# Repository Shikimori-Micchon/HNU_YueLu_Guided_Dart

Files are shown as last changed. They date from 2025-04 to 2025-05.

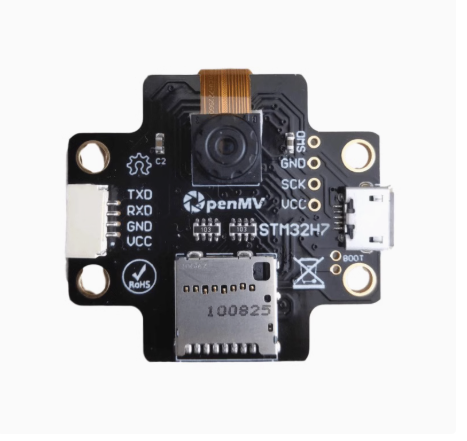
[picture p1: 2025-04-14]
HARDWARE/Module_Page/e43b961c20ee5a998ea4afd373d518cd.png

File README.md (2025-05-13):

# 湖南大学跃鹿战队 制导飞镖开源

## 硬件层

<font size = 4>

* 镖体构型在经过许多尝试后，最终决定使用**X**布局的四舵面空气舵导弹构型，适配长空御风战队22年开源飞镖发射架
* 尾部使用涵道推进增加动力，对控制无太大作用，涵道使用2s 14000kv的群汐涵道
* 数据回传使用匿名数传
* IMU使用维特智能的JY61P
* 视觉识别部分尝试过使用FPGA,但稳定性欠佳，修改麻烦，最后仍使用openmv作为识别模块
* 舵机使用蓝剑舵机
* 电池使用规则参数限制下的最高规格电池

## 软件层

* 主要工作流程为：由IMU检测是否发射，发射后，全程开启涵道定速输出，非制导段进行滚转通道控制，使得滚转为0，进入制导段后，运行PNG任务开始制导，结束任务采用计时一段时间，关闭电机输出，结束所有任务

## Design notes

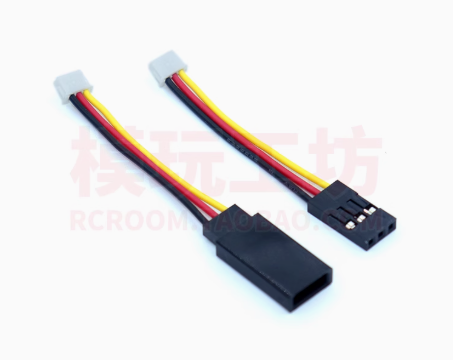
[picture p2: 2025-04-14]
HARDWARE/Module_Page/19b840116ca43cf2742b4f740f94c447.png

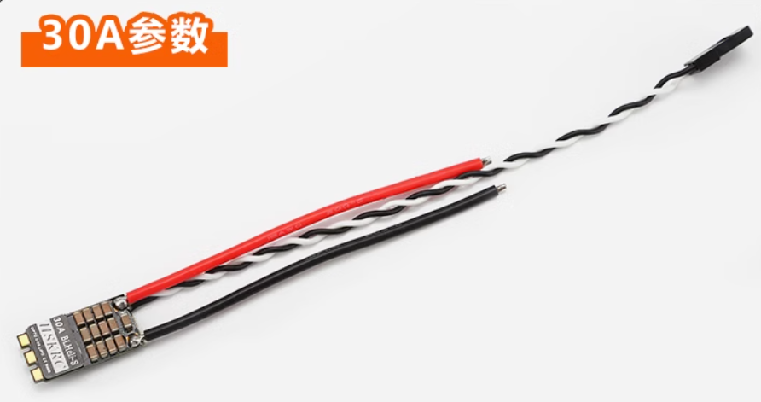
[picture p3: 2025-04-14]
HARDWARE/Module_Page/85e3709fd677be6ccaf7d40ead1b9f13.png

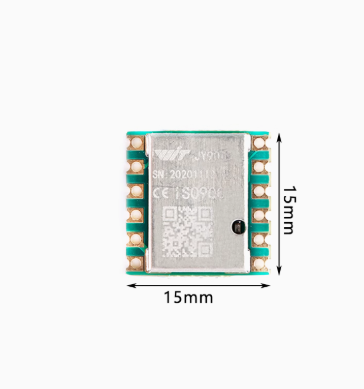
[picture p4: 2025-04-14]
HARDWARE/Module_Page/856e45044ca5f4a56a75f28136125708.png

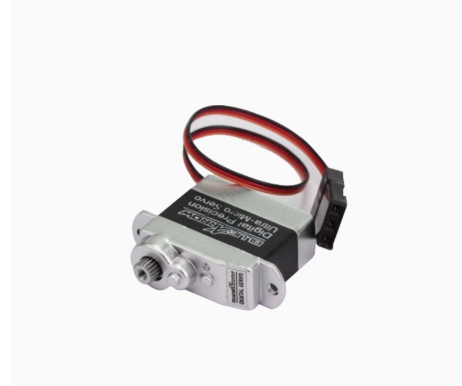
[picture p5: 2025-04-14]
HARDWARE/Module_Page/9cd33fde244de9c2e4ef2b91e4226b22.png

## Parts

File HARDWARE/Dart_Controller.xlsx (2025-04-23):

Comment | Description | Designator | Footprint | LibRef | Quantity
XT30UPB-M | 公头(立式) | BAT | XT30UPB-M | XT30UPB-M | 1
3000Hz | 蜂鸣器 | BUZZER1 | BUZ-TH_BD9.6-P5.00-D0.7-FD | 3000Hz | 1
10nf/0603 | 贴片电容 | C1, C27 | C 0603_M | C 0603 | 2
10uf/0805 | 贴片电容 | C2, C8 | C 0805_M | C 0805 | 2
0.1uf/0805 | 贴片电容 | C3 | C 0805_M | C 0805 | 1
47uf/1206 | 贴片电容 | C4, C5, C6, C7 | C 1206_M | C 1206 | 4
22uf/0805 | 贴片电容 | C9 | C 0805_M | C 0805 | 1
100nf/0603 | 贴片电容 | C10, C11, C14, C17, C18, C19, C20, C22, C23, C24, C25, C26 | C 0603_M | C 0603 | 12
20pf/0603 | 贴片电容 | C12, C13 | C 0603_M | C 0603 | 2
2.2uf/0603 | 贴片电容 | C15, C16 | C 0603_M | C 0603 | 2
10uf/0603 | 贴片电容 | C21 | C 0603_M | C 0603 | 1
SMAJ28CA | 双向瞬态电压抑制二极管 | D1 | SMA | SMAJ28CA | 1
SMF5.0CA | 双向瞬态电压抑制二极管 | D2 | SOD-123FL_L2.8-W1.8-LS3.7-BI | SMF5.0CA | 1
SS34 | 肖特基二极管 | D3 | SMA | SS34 | 1
LED | 发光二极管 | D4, D5 | LED0603-RD_RED | LED_R | 2
1N4148 | 开关二极管 | D6 | SOD-323_L1.8-W1.3-LS2.5-RD | 1N4148WS | 1
固定孔 | 固定孔 | H1, H2, H3, H4 | 铜柱孔 | 铜柱孔 | 4
XT30UPB-F | 母头(立式) | Head_LED, Motor | XT30UPB-F | XT30UPB-F | 2
Header 4 | Header, 4-Pin | JP1, JP2 | HDR2.54-LI-4P | Header 4 | 2
ZH1.5-LS | ZH1.5-LS | JP3, JP4, JP5, JP6, JP8, JP9 | ZH1.5 | ZH1.5-LS | 6
Header 2 | Header, 2-Pin | JP10 | HDR2.54-LI-2P | Header 2 | 1
FXL0630-150-M | 功率电感 | L1 | L-SMD-0630 | FXL0630-150-M | 1
SS8050 | 高频放大-NPN型 | Q1, Q3 | SOT23-3L | SS8050-SMD | 2
WSD30L120DN56 | P沟道场效应管 | Q2 | POWERVDFN-8_L6.0-W5.0-P1.27-BL | WSD30L120DN56 | 1
1K/0603 | 贴片电阻 | R1, R2, R10, R14, R17 | R 0603_M | R 0603 | 5
12K/0603 | 贴片电阻 | R3 | R 0603_M | R 0603 | 1
3.9K/0603 | 贴片电阻 | R4 | R 0603_M | R 0603 | 1
10K/0603 | 贴片电阻 | R5, R6, R7, R9, R18 | R 0603_M | R 0603 | 5
510R/0603 | 贴片电阻 | R8 | R 0603_M | R 0603 | 1
4.7K/0603 | 贴片电阻 | R11, R13 | R 0603_M | R 0603 | 2
47R/0603 | 贴片电阻 | R12 | R 0603_M | R 0603 | 1
2.2K/0603 | 贴片电阻 | R15, R16 | R 0603_M | R 0603 | 2
3x6x5 | 3x6轻触开关 | RESET | TSW SMD-3*6*2.5 | TSW 3x6 | 1
SS-12D10L5 | 滑动开关 | SW2 | SW-TH_SS-12D10L5 | SS-12D10L5 | 1
MX1.25-LS | MX1.25-LS | SWD | MX 1.25-LS-4P | MX1.25-LS | 1
TPS5430DDAR | 降压芯片 | U1 | ESOP8 | TPS5430DDAR | 1
AMS1117-3.3V | LDO | U2 | SOT-89 | AMS1117-3.3V(SOT-89) | 1
STM32F405RGT6 | ARM Cortex-M4 32-bit MCU+FPU, 210 DMIPS, 1024 kB Flash, 192 kB Internal RAM, 51 I/Os, 64-pin LQFP, -40 to 85 degC, Tray | U3 | LQFP64 10x10_N | STM32F405RGT6 | 1
MPU925 | MPU925 | U4 | JY901B_MPU9250 | IMU | 1
TLV9062IDR | 运算放大器 | U5 | SOP8_N | TLV9062IDR | 1
Digital_Transfer | 数传 | U6 | Digital_Transfer | Digital_Transfer | 1
GH1.25-4P-LS | GH1.25-4P-LS | UART | GH1.25-LS-4P | GH1.25-4P-LS | 1
12MHz | 无源晶振/外接20pf负载电容 | XT1 | XTAL_3225_4P | X322512MSB4SI | 1

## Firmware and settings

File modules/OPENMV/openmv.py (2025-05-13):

# Untitled - By: HUAWEI - Sat Apr 12 2025
G_TH = (54, 100, -128, -15, -128, 123)
import sensor, image, time, math
from machine import UART
EXPOSURE_TIME_SCALE = 0.3
sensor.reset()
sensor.set_pixformat(sensor.RGB565)
sensor.set_framesize(sensor.QVGA)  # 320 x240

sensor.set_auto_gain(False)
sensor.set_auto_whitebal(False)

sensor.skip_frames(500)

current_exposure_time_in_microseconds = sensor.get_exposure_us()
print("Current Exposure == %d" % current_exposure_time_in_microseconds)

sensor.set_auto_exposure(False, \
    exposure_us = int(current_exposure_time_in_microseconds * EXPOSURE_TIME_SCALE))
print("New exposure == %d" % sensor.get_exposure_us())

uart = UART(3,115200)

clock = time.clock()

# 定义通信协议
FRAME_HEAD = 0xAA    # 帧头
FRAME_END = 0x55     # 帧尾

def find_led_ring(img):
    bright_blobs = img.find_blobs([(0, 98, -71, -24, 11, 68)],
                                  x_stride=1, y_stride=1)

    for bb in bright_blobs:
        # 计算blob的实际边界
        x_end = bb.x() + bb.w()
        y_end = bb.y() + bb.h()

        # 定义环形检测区域（排除中心过曝区）
        margin = 1
        outer_roi = (
            max(bb.x() + margin, 0),
            max(bb.y() + margin, 0),
            max(bb.w() - 2*margin, 1),  # 保证宽度至少1像素
            max(bb.h() - 2*margin, 1)   # 保证高度至少1像素
        )

#        # 颜色验证
#        outer_stats = img.get_statistics(roi=outer_roi)
#        if not (-70 < outer_stats.a_mean() < -20 and 10 < outer_stats.b_mean() < 40):
#            continue

        # 几何验证（使用实际边界坐标）
        cx, cy = bb.cx(), bb.cy()
        edge_points = []
        for angle in range(0, 360, 30):
            r = bb.w()//4
            x = int(cx + r * math.cos(math.radians(angle)))
            y = int(cy + r * math.sin(math.radians(angle)))

            # 验证点是否在blob区域内
            if (bb.x() <= x < x_end) and (bb.y() <= y < y_end):
                edge_points.append((x,y))

        # green_count = 0
        # for x,y in edge_points:
        #     pix = img.get_pixel(x,y)
        #     lab = image.rgb_to_lab(pix)
        #     if (G_TH[0] < lab[0] < G_TH[1] and
        #         G_TH[2] < lab[1] < G_TH[3] and
        #         G_TH[4] < lab[2] < G_TH[5]):
        #         green_count +=1

        # if green_count >= 8:
        return bb.cx(), bb.cy()

    # return None

while True:
    clock.tick()
    img = sensor.snapshot()
    img.median(1)
    print(clock.fps())
    print(sensor.get_exposure_us())

    result = find_led_ring(img)
    if result:
        cx, cy = result
        img.draw_cross(cx, cy, size=20, color=(255, 0, 0))
        print(f"LED中心: ({cx},{cy})")
        cx_high = (cx >> 8) & 0xFF  # 高字节
        cx_low = cx & 0xFF         # 低字节
        cy_high = (cy >> 8) & 0xFF  # 高字节
        cy_low = cy & 0xFF         # 低字节

        # 构建数据帧
        checksum = (cx_high + cx_low + cy_high + cy_low) & 0xFF
        data_packet = bytearray([
            FRAME_HEAD,
            cx_high, cx_low,
            cy_high, cy_low,
            checksum,
            FRAME_END
        ])
        uart.write(data_packet)
        # print(f"Sent: {[hex(b) for b in data_packet]}")
    else:
        checksum = (0) & 0xFF
        data_packet = bytearray([
            FRAME_HEAD,
            0, 0,
            0, 0,
            checksum,
            FRAME_END
        ])
        uart.write(data_packet)
        # print("未检测到LED环")

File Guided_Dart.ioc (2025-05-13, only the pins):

Mcu.UserName=STM32F405RGTx
PA0-WKUP.Signal=GPIO_Output
PA10.Signal=S_TIM1_CH3
PA11.Signal=S_TIM1_CH4
PA13.Signal=SYS_JTMS-SWDIO
PA14.Signal=SYS_JTCK-SWCLK
PA4.Signal=GPIO_Output
PA8.Signal=S_TIM1_CH1
PA9.Signal=S_TIM1_CH2
PB10.Signal=USART3_TX
PB11.Signal=USART3_RX
PB3.Signal=S_TIM2_CH2
PB6.Signal=USART1_TX
PB7.Signal=USART1_RX
PH0-OSC_IN.Signal=RCC_OSC_IN
PH1-OSC_OUT.Signal=RCC_OSC_OUT

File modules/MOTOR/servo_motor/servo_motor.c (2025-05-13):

#include "servo_motor.h"
#include <stdint.h>

void Servo_Motor_Init(void)
{
    HAL_TIM_PWM_Start(&htim1, TIM_CHANNEL_1);
    HAL_TIM_PWM_Start(&htim1, TIM_CHANNEL_2); 
    HAL_TIM_PWM_Start(&htim1, TIM_CHANNEL_3);
    HAL_TIM_PWM_Start(&htim1, TIM_CHANNEL_4);
    Servo_Motor_SetAngle(0, 0, 0, 0); // 初始化舵机角度
    DWT_Delay_ms(500);
    Servo_Motor_SetAngle(30, 30, 30, 30); // 初始化舵机角度
    DWT_Delay_ms(500);
    Servo_Motor_SetAngle(-30, -30, -30, -30); // 初始化舵机角度
    DWT_Delay_ms(500);
    Servo_Motor_SetAngle(0, 0, 0, 0); // 初始化舵机角度
}
void angle_to_pwm(int16_t angle,  uint16_t*pwm)
{
    if (angle < -60 || angle > 60) {
        return; // Invalid angle
    }
    *pwm = (uint16_t)(angle * 10 + 1500); // Convert angle to PWM value
}

void Servo_Motor_Task(int16_t angle1, int16_t angle2, int16_t angle3, int16_t angle4)
{
    uint16_t pwm1, pwm2, pwm3, pwm4;
    angle_to_pwm(angle1, &pwm1);
    angle_to_pwm(angle2, &pwm2);
    angle_to_pwm(angle3, &pwm3);
    angle_to_pwm(angle4, &pwm4);
    __HAL_TIM_SetCompare(&htim1, TIM_CHANNEL_1, pwm1);
    __HAL_TIM_SetCompare(&htim1, TIM_CHANNEL_2, pwm2);
    __HAL_TIM_SetCompare(&htim1, TIM_CHANNEL_3, pwm3);
    __HAL_TIM_SetCompare(&htim1, TIM_CHANNEL_4, pwm4);
}

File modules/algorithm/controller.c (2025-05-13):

/**
 * @file controller.c
 * @author wanghongxi
 * @author modified by neozng
 * @brief  PID控制器定义
 * @version beta
 * @date 2022-11-01
 *
 * @copyrightCopyright (c) 2022 HNU YueLu EC all rights reserved
 */
#include "controller.h"
#include "memory.h"

/* ----------------------------下面是pid优化环节的实现---------------------------- */

// 梯形积分
static void f_Trapezoid_Intergral(PIDInstance *pid)
{
    // 计算梯形的面积,(上底+下底)*高/2
    pid->ITerm = pid->Ki * ((pid->Err + pid->Last_Err) / 2) * pid->dt;
}

// 变速积分(误差小时积分作用更强)
static void f_Changing_Integration_Rate(PIDInstance *pid)
{
    if (pid->Err * pid->Iout > 0)
    {
        // 积分呈累积趋势
        if (abs(pid->Err) <= pid->CoefB)
            return; // Full integral
        if (abs(pid->Err) <= (pid->CoefA + pid->CoefB))
            pid->ITerm *= (pid->CoefA - abs(pid->Err) + pid->CoefB) / pid->CoefA;
        else // 最大阈值,不使用积分
            pid->ITerm = 0;
    }
}

static void f_Integral_Limit(PIDInstance *pid)
{
    static float temp_Output, temp_Iout;
    temp_Iout = pid->Iout + pid->ITerm;
    temp_Output = pid->Pout + pid->Iout + pid->Dout;
    if (abs(temp_Output) > pid->MaxOut)
    {
        if (pid->Err * pid->Iout > 0) // 积分却还在累积
        {
            pid->ITerm = 0; // 当前积分项置零
        }
    }

    if (temp_Iout > pid->IntegralLimit)
    {
        pid->ITerm = 0;
        pid->Iout = pid->IntegralLimit;
    }
    if (temp_Iout < -pid->IntegralLimit)
    {
        pid->ITerm = 0;
        pid->Iout = -pid->IntegralLimit;
    }
}

// 微分先行(仅使用反馈值而不计参考输入的微分)
static void f_Derivative_On_Measurement(PIDInstance *pid)
{
    pid->Dout = pid->Kd * (pid->Last_Measure - pid->Measure) / pid->dt;
}

// 微分滤波(采集微分时,滤除高频噪声)
static void f_Derivative_Filter(PIDInstance *pid)
{
    pid->Dout = pid->Dout * pid->dt / (pid->Derivative_LPF_RC + pid->dt) +
                pid->Last_Dout * pid->Derivative_LPF_RC / (pid->Derivative_LPF_RC + pid->dt);
}

// 输出滤波
static void f_Output_Filter(PIDInstance *pid)
{
    pid->Output = pid->Output * pid->dt / (pid->Output_LPF_RC + pid->dt) +
                  pid->Last_Output * pid->Output_LPF_RC / (pid->Output_LPF_RC + pid->dt);
}

// 输出限幅
static void f_Output_Limit(PIDInstance *pid)
{
    if (pid->Output > pid->MaxOut)
    {
        pid->Output = pid->MaxOut;
    }
    if (pid->Output < -(pid->MaxOut))
    {
        pid->Output = -(pid->MaxOut);
    }
}

// 电机堵转检测
static void f_PID_ErrorHandle(PIDInstance *pid)
{
    /*Motor Blocked Handle*/
    if (fabsf(pid->Output) < pid->MaxOut * 0.001f || fabsf(pid->Ref) < 0.0001f)
        return;

    if ((fabsf(pid->Ref - pid->Measure) / fabsf(pid->Ref)) > 0.78f)
    {
        // Motor blocked counting
        pid->ERRORHandler.ERRORCount++;
    }
    else
    {
        pid->ERRORHandler.ERRORCount = 0;
    }

    if (pid->ERRORHandler.ERRORCount > 500)
    {
        // Motor blocked over 1000times
        pid->ERRORHandler.ERRORType = PID_MOTOR_BLOCKED_ERROR;
    }
    
}

/* ---------------------------下面是PID的外部算法接口--------------------------- */

/**
 * @brief 初始化PID,设置参数和启用的优化环节,将其他数据置零
 *
 * @param pid    PID实例
 * @param config PID初始化设置
 */
void PIDInit(PIDInstance *pid, PID_Init_Config_s *config)
{
    // config的数据和pid的部分数据是连续且相同的的,所以可以直接用memcpy
    // @todo: 不建议这样做,可扩展性差,不知道的开发者可能会误以为pid和config是同一个结构体
    // 后续修改为逐个赋值
    memset(pid, 0, sizeof(PIDInstance));
    // utilize the quality of struct that its memeory is continuous
    memcpy(pid, config, sizeof(PID_Init_Config_s));
    // set rest of memory to 0
    DWT_GetDeltaT(&pid->DWT_CNT);
}

/**
 * @brief          PID计算
 * @param[in]      PID结构体
 * @param[in]      测量值
 * @param[in]      期望值
 * @retval         返回空
 */
float PIDCalculate(PIDInstance *pid, float measure, float ref)
{
    // 堵转检测
    if (pid->Improve & PID_ErrorHandle)
        f_PID_ErrorHandle(pid);

    pid->dt = DWT_GetDeltaT(&pid->DWT_CNT); // 获取两次pid计算的时间间隔,用于积分和微分

    // 保存上次的测量值和误差,计算当前error
    pid->Measure = measure;
    pid->Ref = ref;
    pid->Err = pid->Ref - pid->Measure;

    // 如果在死区外,则计算PID
    if (abs(pid->Err) > pid->DeadBand)
    {
        // 基本的pid计算,使用位置式
        pid->Pout = pid->Kp * pid->Err;
        pid->ITerm = pid->Ki * pid->Err * pid->dt;
        pid->Dout = pid->Kd * (pid->Err - pid->Last_Err) / pid->dt;

        // 梯形积分
        if (pid->Improve & PID_Trapezoid_Intergral)
            f_Trapezoid_Intergral(pid);
        // 变速积分
        if (pid->Improve & PID_ChangingIntegrationRate)
            f_Changing_Integration_Rate(pid);
        // 微分先行
        if (pid->Improve & PID_Derivative_On_Measurement)
            f_Derivative_On_Measurement(pid);
        // 微分滤波器
        if (pid->Improve & PID_DerivativeFilter)
            f_Derivative_Filter(pid);
        // 积分限幅
        if (pid->Improve & PID_Integral_Limit)
            f_Integral_Limit(pid);

        pid->Iout += pid->ITerm;                         // 累加积分
        pid->Output = pid->Pout + pid->Iout + pid->Dout; // 计算输出

        // 输出滤波
        if (pid->Improve & PID_OutputFilter)
            f_Output_Filter(pid);

        // 输出限幅
        f_Output_Limit(pid);
    }
    else // 进入死区, 则清空积分和输出
    {
        pid->Output = 0;
        pid->ITerm = 0;
    }

    // 保存当前数据,用于下次计算
    pid->Last_Measure = pid->Measure;
    pid->Last_Output = pid->Output;
    pid->Last_Dout = pid->Dout;
    pid->Last_Err = pid->Err;
    pid->Last_ITerm = pid->ITerm;

    return pid->Output;
}

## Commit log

2025-04-23 修改launch
2025-04-23 添加DSP和RTOS
2025-04-23 添加bsp和modules
2025-04-23 添加APP
    [Dart_Controller.PrjPcb, Dart_Controller.xlsx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]
2025-04-24 imu编译成功
2025-04-24 测试IMU
2025-04-26 开启串口1
2025-04-27 DMA收到错误数据
2025-04-27 DMA收到正确数据
2025-04-27 IMU调试成功
2025-04-29 开启电机和舵机
2025-05-13 实现了基于6轴IMU和单目相机的三维PNG
2025-05-13 完成app编写
2025-05-13 硬件最终版本
    [Dart_Controller_SCH.SchDoc, Dart_Controller_SCH2.SchDoc, Dart_Controller_Schlib.SchLib]
